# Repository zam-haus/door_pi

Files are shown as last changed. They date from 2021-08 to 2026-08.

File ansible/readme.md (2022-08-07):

# Usage (run as root):
* configure raspi image file (add ssh file in boot partition and add ssh public key to authorized keys file for root and pi user):

		ansible-playbook setup-rpi-image.yml -e file=/home/USER/Downloads/2022-04-04-raspios-bullseye-arm64-lite.img -e key=/home/USER/.ssh/id_rsa.pub -e host=HOSTNAME
Note: /dev/loop0 is used as hard-coded loopback device

* write disk image to sdcard:

		dd if=/home/USER/Downloads/2022-04-04-raspios-bullseye-arm64-lite.img of=/dev/DISK status=progress

* configure read only root

		ansible-playbook setup-rpi-readonly.yml -i HOSTNAME,
Note: the extra comma at the end is not a mistake

* setup client

		ansible-playbook setup-client.yml -i HOSTNAME,

* update client

		ansible-playbook update-client.yml -i HOSTNAME,

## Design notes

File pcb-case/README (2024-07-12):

PI case inspired by https://www.printables.com/de/model/270114-raspberry-pi-4-case

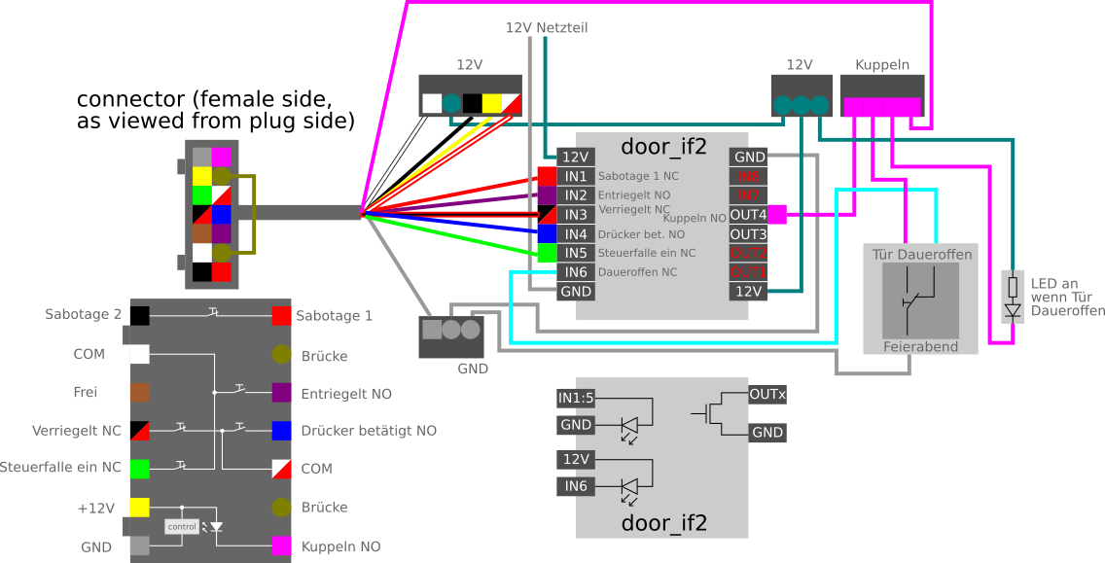
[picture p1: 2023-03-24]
pcb/door_if2/connection-plan-w.switch.png

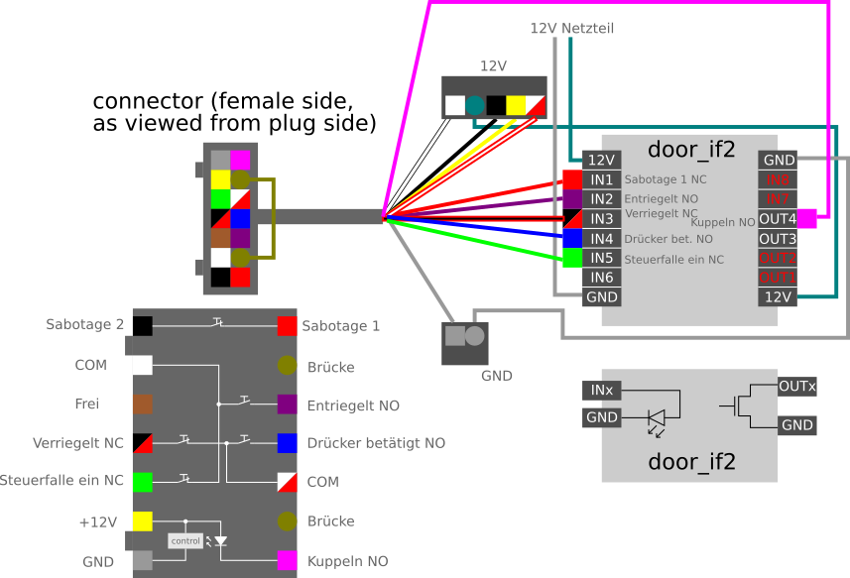
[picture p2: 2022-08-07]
pcb/door_if3_usb/connection-plan.png

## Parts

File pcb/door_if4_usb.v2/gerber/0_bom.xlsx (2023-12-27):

Comment | Designator | Footprint
LY323DC24 | D2,D10,D12,D18,D3,D5,D13,D4,D11 | D_SOD-323
D | D28,D31,D34,D27,D35,D33,D30,D39,D37,D29,D38,D32,D41,D40,D26,D36 | D_SOD-523
SS24B | D24,D7,D22,D9,D16,D25,D8,D23,D17,D14,D15,D6 | D_SMB
10k | R8,R38,R21,R39,R5,R10,R29,R9,R45,R7,R31,R12,R11,R13,R30,R26,R27,R42,R3,R19,R33,R44,R32,R41,R6,R28,R40,R43 | R_0402_1005Metric
2k2 | R60,R54,R17,R55,R20,R49,R66,R52,R64,R56,R47,R18,R16,R46,R57,R63,R68,R15,R50,R48,R14,R62,R65,R58 | R_0402_1005Metric
120 | R22,R4,R2,R24,R36,R34 | R_0402_1005Metric
LTV-247 | U3,U7,U8,U4,U2,U6,U5 | SOP-16_4.4x10.4mm_P1.27mm
IRF7343 | Q4,Q6,Q1,Q5,Q2,Q3 | SO-8_3.9x4.9mm_P1.27mm
100n/50V | C3,C2,C4,C1 | C_0805_2012Metric
LED | D1 | LED_0603_1608Metric
COS2171 | U10,U9 | SOP-8_3.9x4.9mm_P1.27mm
470 | R1 | R_0402_1005Metric

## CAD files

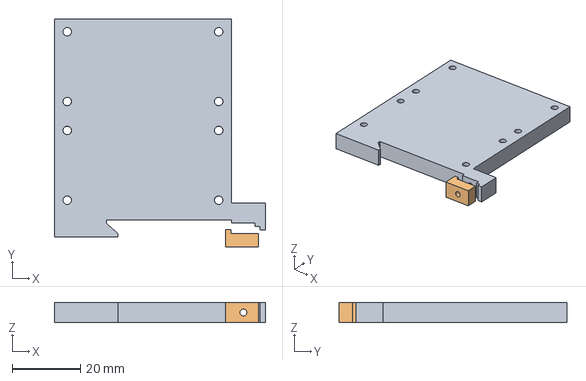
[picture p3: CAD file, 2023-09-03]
extensions/relais/relais_mount.FCStd
62.0 x 67.0 x 6.00 mm
Plate
CounterBlock

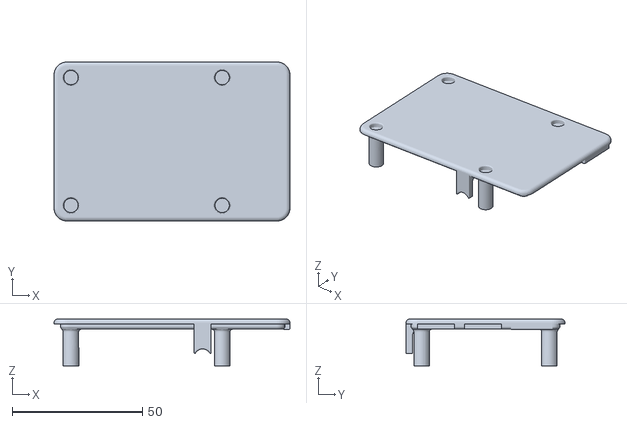
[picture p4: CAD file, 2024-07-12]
pcb-case/General_lit.stl
90.5 x 61.0 x 18.0

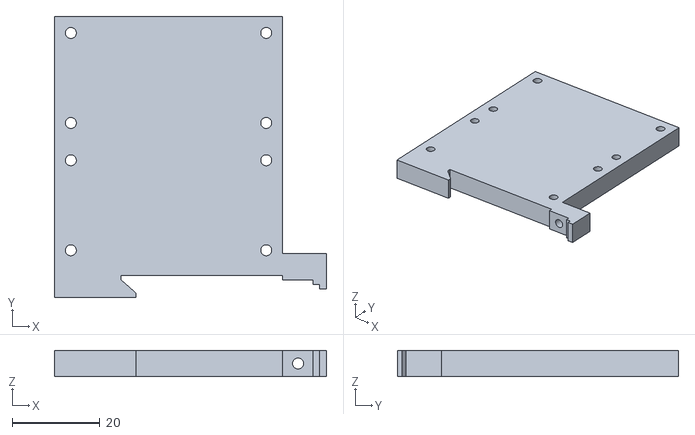
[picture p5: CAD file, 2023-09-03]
extensions/relais/relais_mount-Plate.stl
62.0 x 64.0 x 6.00

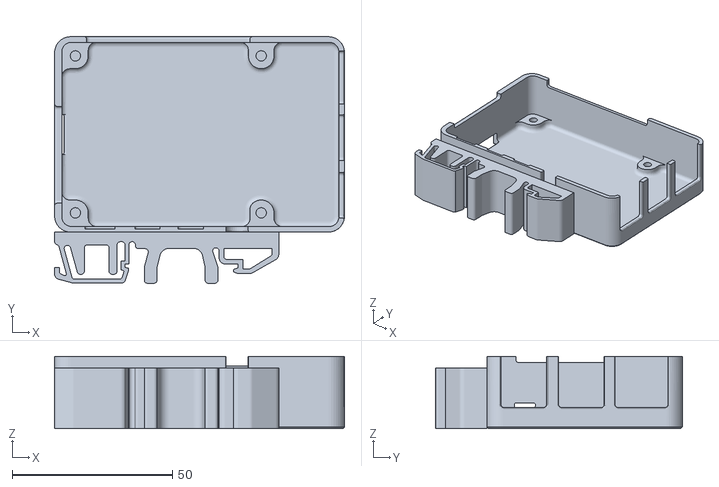
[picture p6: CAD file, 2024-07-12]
pcb-case/Pi4_DIN_case.stl
90.5 x 77.0 x 22.6

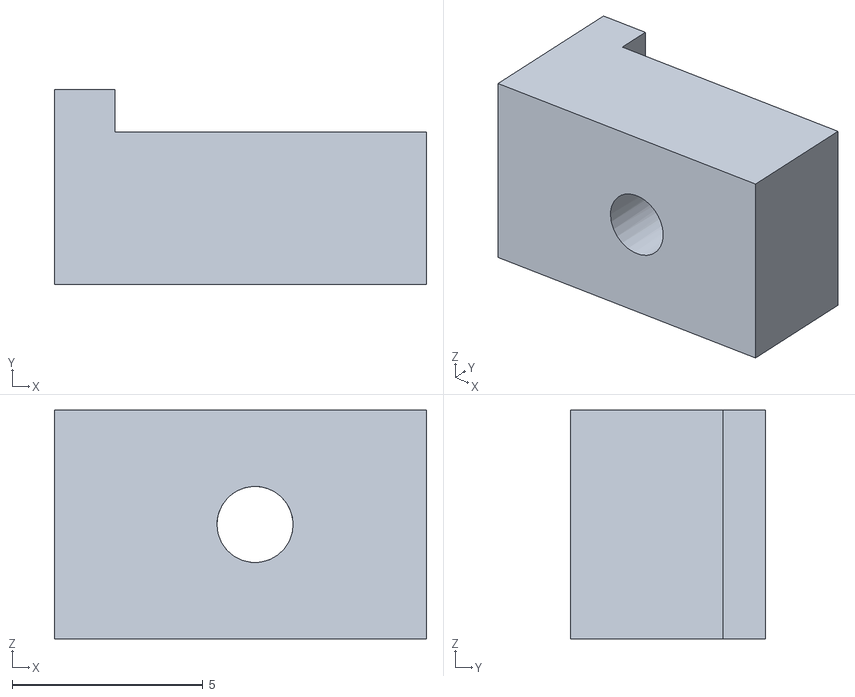
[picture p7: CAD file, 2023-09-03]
extensions/relais/relais_mount-CounterBlock.stl
9.76 x 5.12 x 6.00

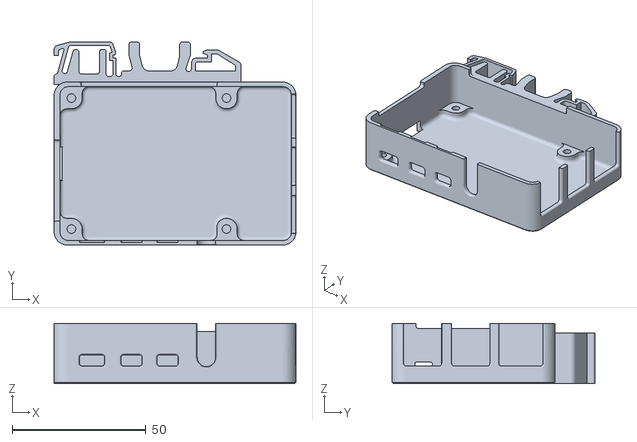
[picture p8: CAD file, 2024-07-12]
pcb-case/Pi4_DIN_case_2.stl
90.5 x 76.0 x 22.6

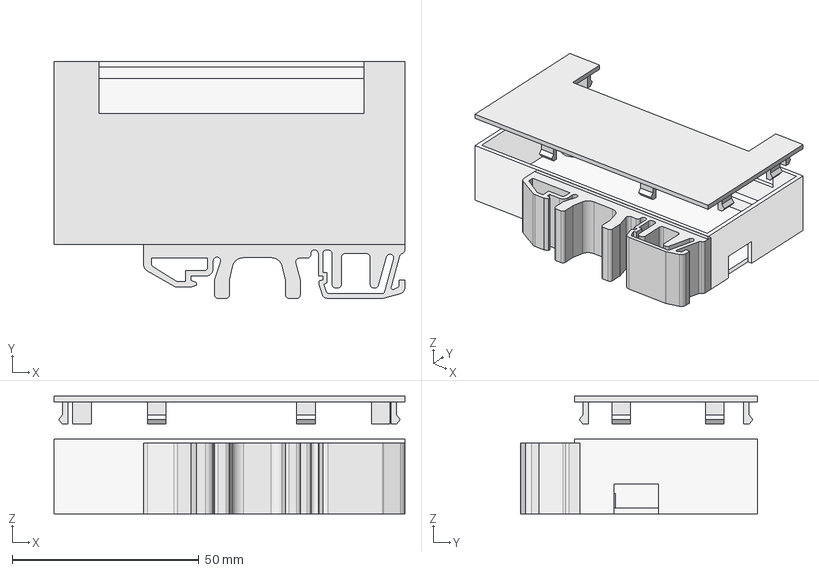
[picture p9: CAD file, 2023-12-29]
pcb-case/if4-usb-case.v2.FCStd
94.0 x 63.5 x 31.5 mm
Body-main
Body-clip
Body-top-complete

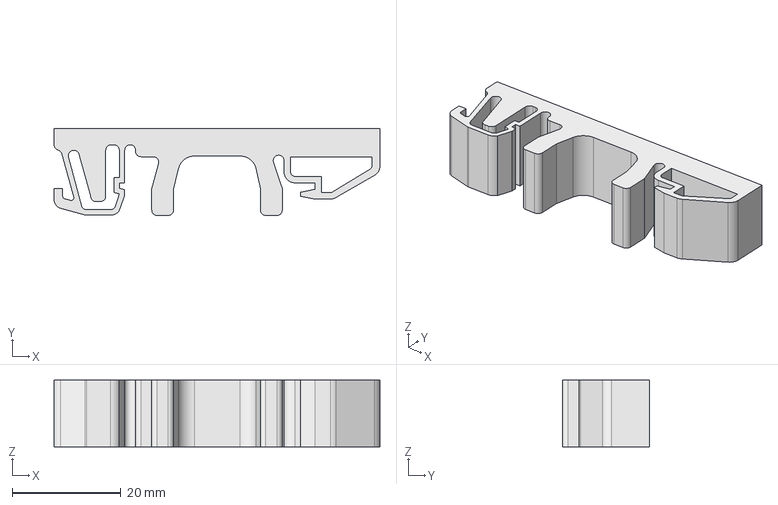
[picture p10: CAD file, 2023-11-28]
pcb-case/DINrail_Clip.fcstd
60.0 x 16.0 x 12.3 mm

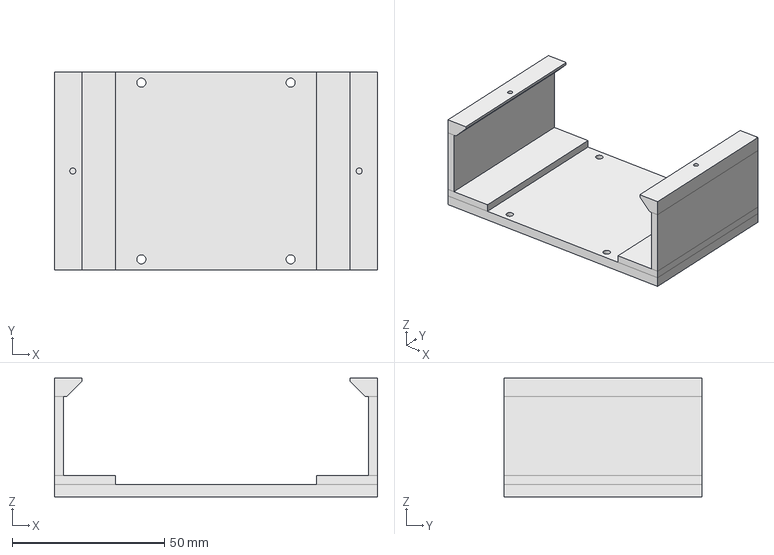
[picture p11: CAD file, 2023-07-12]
pcb-case/raspi-hub-case.FCStd
106.0 x 65.0 x 39.0 mm

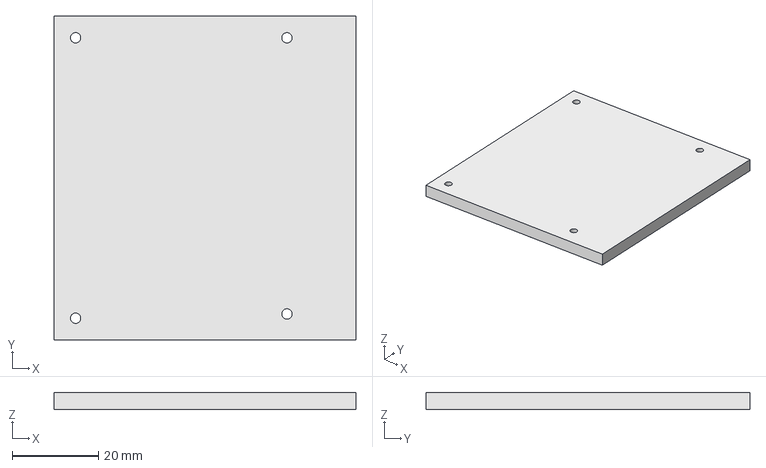
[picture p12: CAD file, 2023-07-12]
pcb-case/if3-usb-case.FCStd
70.0 x 75.0 x 4.00 mm

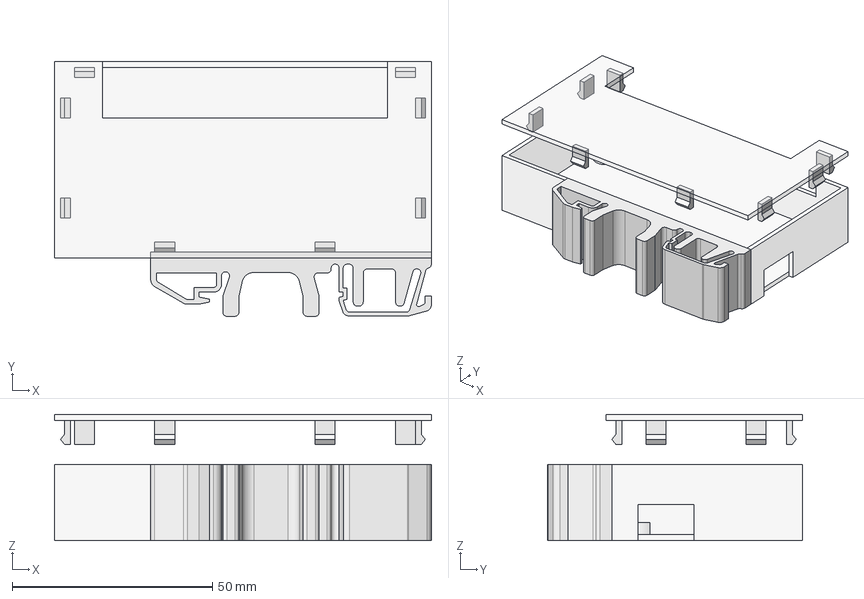
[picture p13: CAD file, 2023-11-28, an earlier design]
pcb-case/if4-usb-case.FCStd
94.0 x 63.5 x 31.5 mm
Body-main
Body-clip
Body-top
Body-top-clip
Body-top-clip-2
Body-top-clip-3
Body-top-clip-4
Body-top-clip-5
Body-top-clip-6
Body-top-clip-7
Body-top-clip-8

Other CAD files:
pcb-case/DINrail_Clip.stl
pcb-case/if4-usb-case.v2.stl

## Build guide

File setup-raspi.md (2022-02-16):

# Raspi Setup

## Hardware

* Raspberry PI 4B (2 GB)
* PoE+ Hat for RasPi 4 Model B (25 W)
* door_if Hat

## Raspi Configuration

### PoE Fan Control

*/boot/config.txt (section [all]):*

	dtparam=poe_fan_temp0=60000
	dtparam=poe_fan_temp1=65000
	dtparam=poe_fan_temp2=70000
	dtparam=poe_fan_temp3=75000

### Disable WLAN and Bluetooth

*/boot/config.txt (general section):*
	dtoverlay=disable-wifi
	dtoverlay=disable-bt

### Read-Only Filesystem

*according to* [c't 26/2021](https://www.heise.de/select/ct/2021/16/2112313321295857638) 

* install network-manager:

		apt-get install network-manager
		systemctl enable --now NetworkManager
		cd /etc
		ln -sf ../run/NetworkManager/resolv.conf
		
* configure kernel boot in /boot/cmdline.txt
    * ... root=... **ro** rootfstype=ext4 ...
* configure filesystems in /etc/fstab
    * ... /boot vfat ro,defaults ...
    * ... / ext4 ro,defaults,noatime ...
* add tmpfs in /etc/fstab:

		tmpfs           /var/lib/systemd   tmpfs     mode=0755               0 0
		tmpfs           /var/lib/private   tmpfs     mode=0700               0 0
		tmpfs           /var/log           tmpfs     nodev,nosuid            0 0
		tmpfs           /var/tmp           tmpfs     nodev,nosuid            0 0
		tmpfs           /var/cache         tmpfs     nodev,nosuid            0 0
		tmpfs           /tmp               tmpfs     nodev,nosuid,mode=1777  0 0

* disable swap

		systemctl disable dphys-swapfile

* shell highlighting /root/.bashrc

		export LS_OPTIONS='--color=auto'
		eval "`dircolors`"
		alias ls='ls $LS_OPTIONS'
		alias ll='ls $LS_OPTIONS -la'
		alias l='ls $LS_OPTIONS'
		set_bash_prompt() {
			fs_mode=$(mount | sed -n -e "s/^\/dev\/.* on \/ .*(\(r[w|o]\).*/\1/p")
			PS1='\[\033[01;31m\]\u@\h${fs_mode:+($fs_mode)}\[\033[00m\]:\[\033[01;34m\]\w\[\033[00m\]\$ '
		}
		alias ro='sudo mount -o remount,ro / ; sudo mount -o remount,ro /boot'
		alias rw='sudo mount -o remount,rw / ; sudo mount -o remount,rw /boot'
		PROMPT_COMMAND=set_bash_prompt

* shell highlighting /home/pi/.bashrc

		export LS_OPTIONS='--color=auto'
		eval "`dircolors`"
		alias ls='ls $LS_OPTIONS'
		alias ll='ls $LS_OPTIONS -la'
		alias l='ls $LS_OPTIONS'
		set_bash_prompt() {
			fs_mode=$(mount | sed -n -e "s/^\/dev\/.* on \/ .*(\(r[w|o]\).*/\1/p")
			PS1='\[\033[01;32m\]\u@\h${fs_mode:+($fs_mode)}\[\033[00m\]:\[\033[01;34m\]\w\[\033[00m\]\$ '
		}
		alias ro='sudo mount -o remount,ro / ; sudo mount -o remount,ro /boot'
		alias rw='sudo mount -o remount,rw / ; sudo mount -o remount,rw /boot'
		PROMPT_COMMAND=set_bash_prompt

### Setup Door Manager on Raspi

* install python3-pip and pipenv

		sudo apt install python3-pip
		sudo pip3 install pipenv

* copy door_manager dir to /home/pi

* copy door_manager/config.json.example to door_manager/config.json

* adjust config.json settings according to your setup

* setup pipenv

		cd /home/pi/door_manager
		pipenv install --site-packages

* setup systemd service

		sudo cp /home/pi/door_manager/door-manager.service /etc/systemd/system/
		sudo systemctl daemon-reload
		sudo systemctl enable door-manager
		sudo systemctl start door-manager

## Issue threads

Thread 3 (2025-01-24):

Nach einem Netzwerkausfall gehts nicht mehr (dauerhaft)

cod3monk, 2025-01-24:
Wir hatten heute einen Stromausfall beim Netzwerkzeugs im Haupthaus, der Doorpi im Seminarraum selbst war davon nicht betroffen. Danach ging der Hintereingang nicht mehr per Sesam und kam auch nicht automatisch wieder hoch als Netzwerk wieder funktioniert hatte. Ein powercycle vom doorpi hat geholfen.

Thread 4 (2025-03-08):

Reset des USB Devices wird nicht erkannt

chca42, 2025-03-08:
Der door_manager bleibt hängen, wenn das USB-Device resettet, weil er weder den Reset erkennt noch abstürzt.

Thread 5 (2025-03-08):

Konfiguration verteilt auf USB-HAL und doorpi

TheJonny, 2025-03-08:
Die der picopi in der USB-HAL-Platine hat eine seperate Konfigurationsdatei, wo logisch H/L auf Elektrisch H/L/Z zugeordnet wird. Hier wäre es schön, wenn das nur in der  config.json in door_pi konfiguriert würde, damit sich alle USB-HAL-Platinen gleich immer verhalten.

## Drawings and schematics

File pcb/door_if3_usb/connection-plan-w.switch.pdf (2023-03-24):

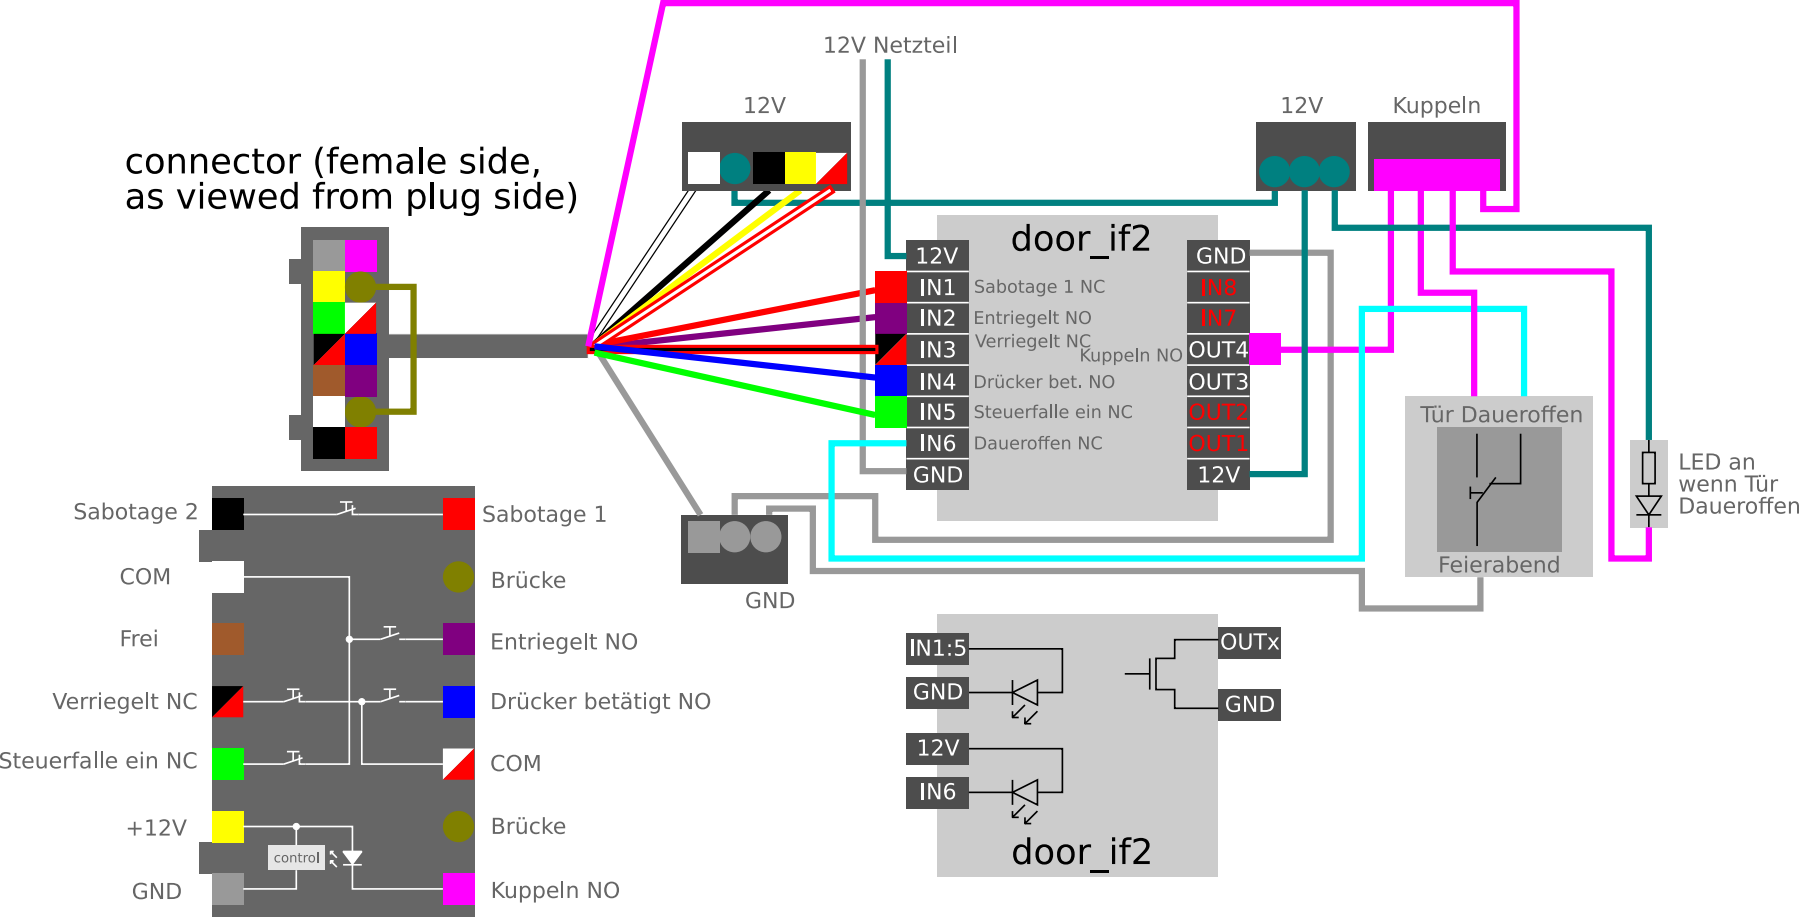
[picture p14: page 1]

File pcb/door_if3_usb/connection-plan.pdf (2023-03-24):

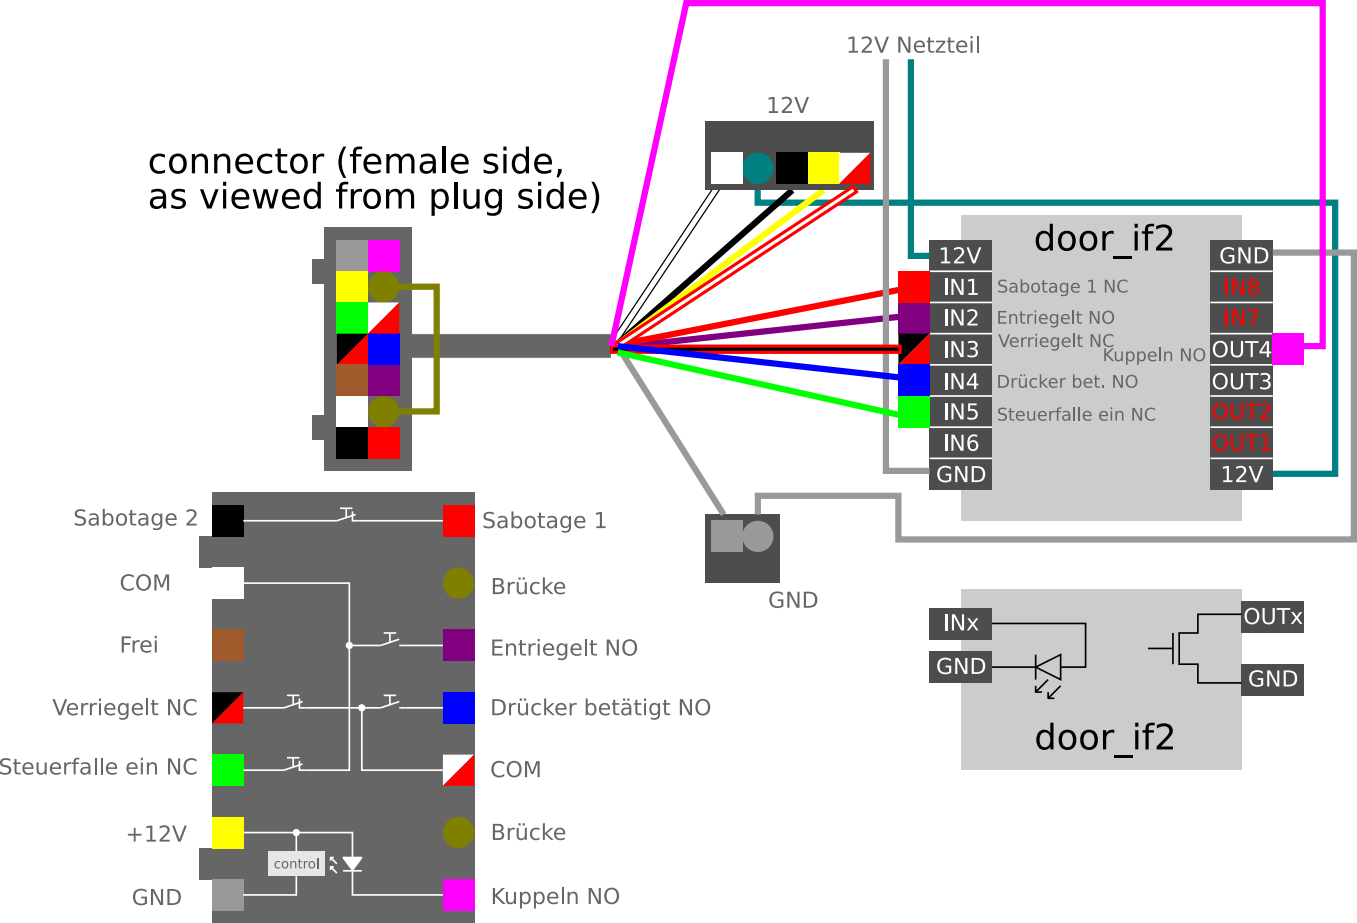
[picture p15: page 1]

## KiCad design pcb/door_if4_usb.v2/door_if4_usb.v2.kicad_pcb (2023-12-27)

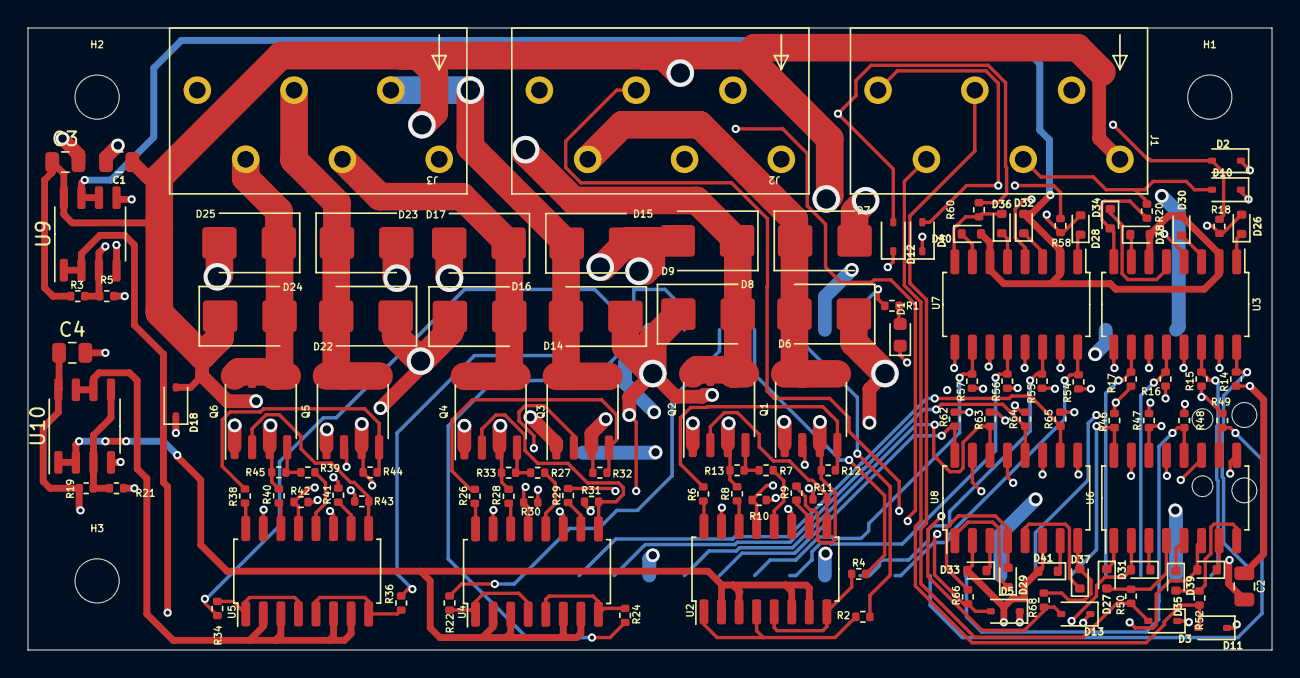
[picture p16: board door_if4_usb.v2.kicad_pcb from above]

Board: 4 copper layers, 90.0 x 45.0 mm, 123 parts (1 on the bottom side), 102 nets.

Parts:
C1, C2, C3, C4: 100n/50V; C_0805_2012Metric
D1: LED; LED_0603_1608Metric
D2, D3, D4, D5, D10, D11, D12, D13, D18: LY323DC24; D_SOD-323
D6, D7, D8, D9, D14, D15, D16, D17, D22, D23, D24, D25: SS24B; D_SMB
D26, D27, D28, D29, D30, D31, D32, D33, D34, D35, D36, D37, D38, D39, D40, D41: D; D_SOD-523
H1, H2, H3: MountingHole; MountingHole_3.2mm_M3_DIN965
J1, J2, J3: WAGO 250-206; WAGO-250-206
Q1, Q2, Q3, Q4, Q5, Q6: IRF7343; SO-8_3.9x4.9mm_P1.27mm
R1: 470; R_0402_1005Metric
R2, R4, R22, R24, R34, R36: 120; R_0402_1005Metric
R3, R5, R6, R7, R8, R9, R10, R11, R12, R13, R19, R21, R26, R27, R28, R29, R30, R31, R32, R33, R38, R39, R40, R41, R42, R43, R44, R45: 10k; R_0402_1005Metric
R14, R15, R16, R17, R18, R20, R46, R47, R48, R49, R50, R52, R54, R55, R56, R57, R58, R60, R62, R63, R64, R65, R66, R68: 2k2; R_0402_1005Metric
U1: Pico; RPi_Pico_SMDonly
U2, U3, U4, U5, U6, U7, U8: LTV-247; SOP-16_4.4x10.4mm_P1.27mm
U9, U10: COS2171; SOP-8_3.9x4.9mm_P1.27mm

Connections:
+3V3: C2.1, C4.1, R14.1, R15.1, R16.1, R17.1, R19.1, R46.1, R47.1, R48.1, R49.1, R54.1, R55.1, R56.1, R57.1, R62.1, R63.1, R64.1, R65.1, U1.36 (3V3), U10.8 (V+)
+24V: C1.1, C3.1, D6.1 (K), D8.1 (K), D14.1 (K), D16.1 (K), D18.2 (A2), D22.1 (K), D24.1 (K), J1.1, J2.1, Q1.3 (S2), Q2.3 (S2), Q3.3 (S2), Q4.3 (S2), Q5.3 (S2), Q6.3 (S2), R3.1, R8.2, R9.2, R12.2, R13.2, R28.2, R29.2, R32.2, R33.2, R40.2, R41.2, R44.2, R45.2, U9.8 (V+)
GND: C2.2, C4.2, D1.1 (K), R21.2, U1.3 (GND), U1.8 (GND), U1.13 (GND), U1.18 (GND), U1.23 (GND), U1.28 (GND), U1.38 (GND), U1.42 (GND), U3.9, U3.11, U3.13, U3.15, U6.9, U6.11, U6.13, U6.15, U7.9, U7.11, U7.13, U7.15, U8.9, U8.11, U8.13, U8.15, U10.4 (V-)
GNDA: C1.2, C3.2, D2.1 (A1), D3.1 (A1), D4.1 (A1), D5.1 (A1), D7.2 (A), D9.2 (A), D10.1 (A1), D11.1 (A1), D12.1 (A1), D13.1 (A1), D15.2 (A), D17.2 (A), D18.1 (A1), D23.2 (A), D25.2 (A), J2.6, J3.6, Q1.1 (S1), Q2.1 (S1), Q3.1 (S1), Q4.1 (S1), Q5.1 (S1), Q6.1 (S1), R5.2, R10.1, R11.1, R30.1, R31.1, R42.1, R43.1, U2.11, U2.15, U4.11, U4.15, U5.11, U5.15, U9.4 (V-)
IN1: D2.2 (A2), J1.2, R18.2
IN2: D10.2 (A2), J1.3, R20.2
IN3: D3.2 (A2), J1.4, R50.2
IN4: D11.2 (A2), J1.5, R52.2
IN5: D4.2 (A2), J1.6, R58.2
IN6: D12.2 (A2), J2.2, R60.2
IN7: D5.2 (A2), J2.3, R66.2
IN8: D13.2 (A2), J2.4, R68.2
unnamed: D1.2 (A), R1.1
unnamed: D26.2 (A), R18.1, U3.4
unnamed: D26.1 (K), U3.1
unnamed: D27.2 (A), R50.1, U6.4
unnamed: D27.1 (K), U6.1
unnamed: D28.2 (A), R58.1, U7.4
unnamed: D28.1 (K), U7.1
unnamed: D29.2 (A), R66.1, U8.4
unnamed: D29.1 (K), U8.1
unnamed: D30.1 (K), U3.3
unnamed: D31.1 (K), U6.3
unnamed: D32.1 (K), U7.3
unnamed: D33.1 (K), U8.3
unnamed: D34.2 (A), R20.1, U3.8
unnamed: D34.1 (K), U3.5
unnamed: D35.2 (A), R52.1, U6.8
unnamed: D35.1 (K), U6.5
unnamed: D36.2 (A), R60.1, U7.8
unnamed: D36.1 (K), U7.5
unnamed: D37.2 (A), R68.1, U8.8
unnamed: D37.1 (K), U8.5
unnamed: D38.1 (K), U3.7
unnamed: D39.1 (K), U6.7
unnamed: D40.1 (K), U7.7
unnamed: D41.1 (K), U8.7
unnamed: Q1.2 (G1), R10.2, U2.13
unnamed: Q1.4 (G2), R6.2, R12.1
unnamed: Q2.2 (G1), R11.2, U2.9
unnamed: Q2.4 (G2), R7.2, R13.1
unnamed: Q3.2 (G1), R30.2, U4.13
unnamed: Q3.4 (G2), R26.2, R32.1
unnamed: Q4.2 (G1), R31.2, U4.9
unnamed: Q4.4 (G2), R27.2, R33.1
unnamed: Q5.2 (G1), R42.2, U5.13
unnamed: Q5.4 (G2), R38.2, R44.1
unnamed: Q6.2 (G1), R43.2, U5.9
unnamed: Q6.4 (G2), R39.2, R45.1
unnamed: R2.2, U2.1, U2.4
unnamed: R4.2, U2.5, U2.8
unnamed: R6.1, U2.16
unnamed: R7.1, U2.12
unnamed: R8.1, U2.14
unnamed: R9.1, U2.10
unnamed: R22.2, U4.1, U4.4
unnamed: R24.2, U4.5, U4.8
unnamed: R26.1, U4.16
unnamed: R27.1, U4.12
unnamed: R28.1, U4.14
unnamed: R29.1, U4.10
unnamed: R34.2, U5.1, U5.4
unnamed: R36.2, U5.5, U5.8
unnamed: R38.1, U5.16
unnamed: R39.1, U5.12
unnamed: R40.1, U5.14
unnamed: R41.1, U5.10
unnamed: R3.2, R5.1, U9.3 (+), U9.5 (+)
unnamed: R19.2, R21.1, U10.3 (+), U10.5 (+)
OUT1: D6.2 (A), D7.1 (K), J2.5, Q1.5 (D), Q1.6 (D), Q1.7 (D), Q1.8 (D)
OUT2: D8.2 (A), D9.1 (K), J3.1, Q2.5 (D), Q2.6 (D), Q2.7 (D), Q2.8 (D)
OUT3: D14.2 (A), D15.1 (K), J3.2, Q3.5 (D), Q3.6 (D), Q3.7 (D), Q3.8 (D)
OUT4: D16.2 (A), D17.1 (K), J3.3, Q4.5 (D), Q4.6 (D), Q4.7 (D), Q4.8 (D)
OUT5: D22.2 (A), D23.1 (K), J3.4, Q5.5 (D), Q5.6 (D), Q5.7 (D), Q5.8 (D)
OUT6: D24.2 (A), D25.1 (K), J3.5, Q6.5 (D), Q6.6 (D), Q6.7 (D), Q6.8 (D)
O_LED: R1.2, U1.29 (GPIO22)
S_IN1A: R14.2, U1.1 (GPIO0), U3.16
S_IN1B: R15.2, U1.2 (GPIO1), U3.14
S_IN2A: R16.2, U1.4 (GPIO2), U3.12
S_IN2B: R17.2, U1.5 (GPIO3), U3.10
S_IN3A: R46.2, U1.6 (GPIO4), U6.16
S_IN3B: R47.2, U1.7 (GPIO5), U6.14
S_IN4A: R48.2, U1.9 (GPIO6), U6.12
S_IN4B: R49.2, U1.10 (GPIO7), U6.10
S_IN5A: R54.2, U1.11 (GPIO8), U7.16
S_IN5B: R55.2, U1.12 (GPIO9), U7.14
S_IN6A: R56.2, U1.14 (GPIO10), U7.12
S_IN6B: R57.2, U1.15 (GPIO11), U7.10
S_IN7A: R62.2, U1.16 (GPIO12), U8.16
S_IN7B: R63.2, U1.17 (GPIO13), U8.14
S_IN8A: R64.2, U1.19 (GPIO14), U8.12
S_IN8B: R65.2, U1.20 (GPIO15), U8.10
S_OUT1: R2.1, U1.27 (GPIO21)
S_OUT2: R4.1, U1.26 (GPIO20)
S_OUT3: R22.1, U1.25 (GPIO19)
S_OUT4: R24.1, U1.24 (GPIO18)
S_OUT5: R34.1, U1.22 (GPIO17)
S_OUT6: R36.1, U1.21 (GPIO16)
VmidA: D31.2 (A), D33.2 (A), D39.2 (A), D41.2 (A), U6.2, U6.6, U8.2, U8.6, U9.1, U9.2 (-)
VmidB: D30.2 (A), D32.2 (A), D38.2 (A), D40.2 (A), U3.2, U3.6, U7.2, U7.6, U9.6 (-), U9.7
Vmid_3v3_A: U2.2, U2.3, U2.6, U2.7, U4.2, U4.3, U4.6, U4.7, U10.1, U10.2 (-)
Vmid_3v3_B: U5.2, U5.3, U5.6, U5.7, U10.6 (-), U10.7

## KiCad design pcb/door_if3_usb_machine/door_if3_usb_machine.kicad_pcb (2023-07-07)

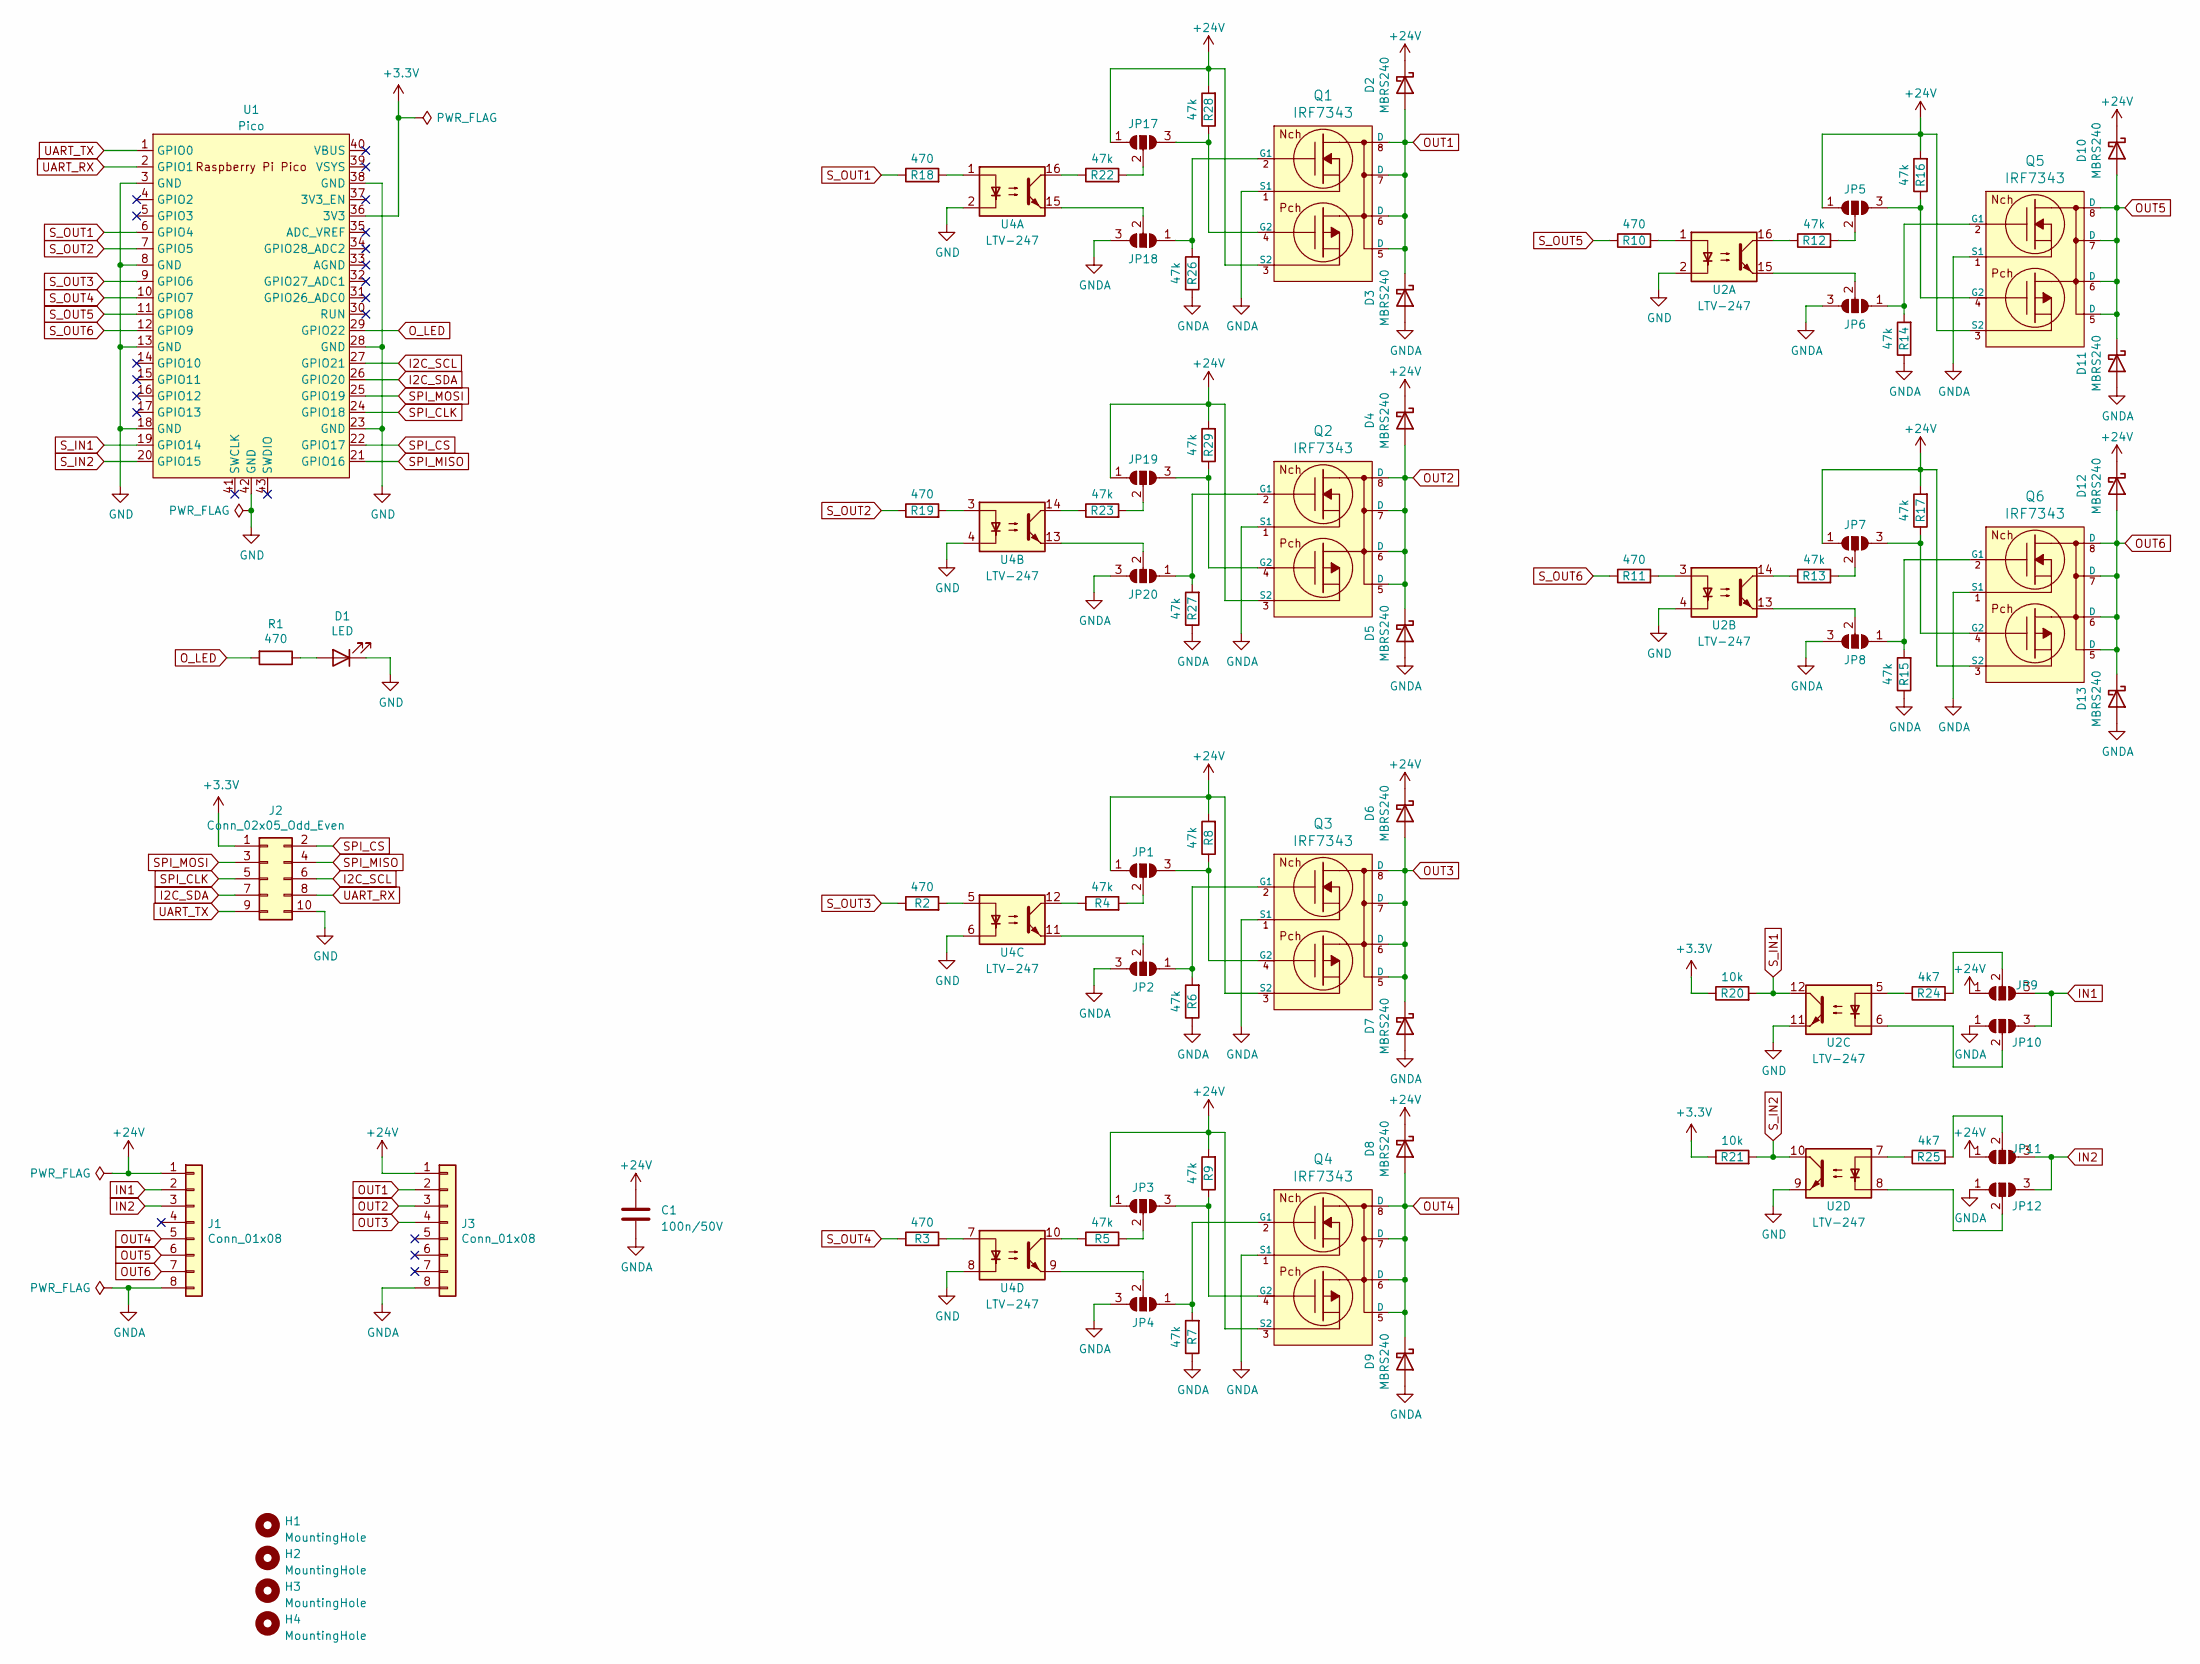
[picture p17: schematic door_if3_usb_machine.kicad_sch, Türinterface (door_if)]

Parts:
C1: 100n/50V; C_0603_1608Metric_Pad1.08x0.95mm_HandSolder
D1: LED; LED_0603_1608Metric_Pad1.05x0.95mm_HandSolder
D2, D3, D4, D5, D6, D7, D8, D9, D10, D11, D12, D13: MBRS240; D_SMB_Handsoldering
H1, H2, H3, H4: MountingHole; MountingHole_3.2mm_M3_DIN965
J1, J3: Conn_01x08; LSA-IDC381-8
J2: Conn_02x05_Odd_Even; con-harting-ml-ML10
JP1, JP2, JP3, JP4, JP5, JP6, JP7, JP8, JP9, JP10, JP11, JP12, JP17, JP18, JP19, JP20: SolderJumper_3_Open; SolderJumper-3_P1.3mm_Open_Pad1.0x1.5mm
Q1, Q2, Q3, Q4, Q5, Q6: IRF7343; SO-8_3.9x4.9mm_P1.27mm
R1, R2, R3, R10, R11, R18, R19: 470; R_0603_1608Metric_Pad0.98x0.95mm_HandSolder
R4, R5, R6, R7, R8, R9, R12, R13, R14, R15, R16, R17, R22, R23, R26, R27, R28, R29: 47k; R_0603_1608Metric_Pad0.98x0.95mm_HandSolder
R20, R21: 10k; R_0603_1608Metric_Pad0.98x0.95mm_HandSolder
R24, R25: 4k7; R_0603_1608Metric_Pad0.98x0.95mm_HandSolder
U1: Pico; RPi_Pico_SMDonly
U2, U4: LTV-247; SOP-16_4.4x10.4mm_P1.27mm

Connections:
+3V3: J2.1, R20.1, R21.1, U1.36 (3V3)
+24V: C1.1, D2.1 (K), D4.1 (K), D6.1 (K), D8.1 (K), D10.1 (K), D12.1 (K), J1.1, J3.1, JP1.1 (A), JP3.1 (A), JP5.1 (A), JP7.1 (A), JP9.1 (A), JP11.1 (A), JP17.1 (A), JP19.1 (A), Q1.3 (S2), Q2.3 (S2), Q3.3 (S2), Q4.3 (S2), Q5.3 (S2), Q6.3 (S2), R8.2, R9.2, R16.2, R17.2, R28.2, R29.2
GND: D1.1 (K), J2.10, U1.3 (GND), U1.8 (GND), U1.13 (GND), U1.18 (GND), U1.23 (GND), U1.28 (GND), U1.38 (GND), U1.42 (GND), U2.2, U2.4, U2.9, U2.11, U4.2, U4.4, U4.6, U4.8
GNDA: C1.2, D3.2 (A), D5.2 (A), D7.2 (A), D9.2 (A), D11.2 (A), D13.2 (A), J1.8, J3.8, JP2.3 (B), JP4.3 (B), JP6.3 (B), JP8.3 (B), JP10.1 (A), JP12.1 (A), JP18.3 (B), JP20.3 (B), Q1.1 (S1), Q2.1 (S1), Q3.1 (S1), Q4.1 (S1), Q5.1 (S1), Q6.1 (S1), R6.1, R7.1, R14.1, R15.1, R26.1, R27.1
I2C_SCL: J2.6, U1.27 (GPIO21)
I2C_SDA: J2.7, U1.26 (GPIO20)
IN1: J1.2, JP9.3 (B), JP10.3 (B)
IN2: J1.3, JP11.3 (B), JP12.3 (B)
unnamed: D1.2 (A), R1.1
unnamed: JP1.3 (B), Q3.4 (G2), R8.1
unnamed: JP1.2 (C), R4.2
unnamed: JP2.1 (A), Q3.2 (G1), R6.2
unnamed: JP2.2 (C), U4.11
unnamed: JP3.3 (B), Q4.4 (G2), R9.1
unnamed: JP3.2 (C), R5.2
unnamed: JP4.1 (A), Q4.2 (G1), R7.2
unnamed: JP4.2 (C), U4.9
unnamed: JP5.3 (B), Q5.4 (G2), R16.1
unnamed: JP5.2 (C), R12.2
unnamed: JP6.1 (A), Q5.2 (G1), R14.2
unnamed: JP6.2 (C), U2.15
unnamed: JP7.3 (B), Q6.4 (G2), R17.1
unnamed: JP7.2 (C), R13.2
unnamed: JP8.1 (A), Q6.2 (G1), R15.2
unnamed: JP8.2 (C), U2.13
unnamed: JP9.2 (C), R24.2
unnamed: JP10.2 (C), U2.6
unnamed: JP11.2 (C), R25.2
unnamed: JP12.2 (C), U2.8
unnamed: JP17.3 (B), Q1.4 (G2), R28.1
unnamed: JP17.2 (C), R22.2
unnamed: JP18.1 (A), Q1.2 (G1), R26.2
unnamed: JP18.2 (C), U4.15
unnamed: JP19.3 (B), Q2.4 (G2), R29.1
unnamed: JP19.2 (C), R23.2
unnamed: JP20.1 (A), Q2.2 (G1), R27.2
unnamed: JP20.2 (C), U4.13
unnamed: R2.2, U4.5
unnamed: R3.2, U4.7
unnamed: R4.1, U4.12
unnamed: R5.1, U4.10
unnamed: R10.2, U2.1
unnamed: R11.2, U2.3
unnamed: R12.1, U2.16
unnamed: R13.1, U2.14
unnamed: R18.2, U4.1
unnamed: R19.2, U4.3
unnamed: R22.1, U4.16
unnamed: R23.1, U4.14
unnamed: R24.1, U2.5
unnamed: R25.1, U2.7
OUT1: D2.2 (A), D3.1 (K), J3.2, Q1.5 (D), Q1.6 (D), Q1.7 (D), Q1.8 (D)
OUT2: D4.2 (A), D5.1 (K), J3.3, Q2.5 (D), Q2.6 (D), Q2.7 (D), Q2.8 (D)
OUT3: D6.2 (A), D7.1 (K), J3.4, Q3.5 (D), Q3.6 (D), Q3.7 (D), Q3.8 (D)
OUT4: D8.2 (A), D9.1 (K), J1.5, Q4.5 (D), Q4.6 (D), Q4.7 (D), Q4.8 (D)
OUT5: D10.2 (A), D11.1 (K), J1.6, Q5.5 (D), Q5.6 (D), Q5.7 (D), Q5.8 (D)
OUT6: D12.2 (A), D13.1 (K), J1.7, Q6.5 (D), Q6.6 (D), Q6.7 (D), Q6.8 (D)
O_LED: R1.2, U1.29 (GPIO22)
SPI_CLK: J2.5, U1.24 (GPIO18)
SPI_CS: J2.2, U1.22 (GPIO17)
SPI_MISO: J2.4, U1.21 (GPIO16)
SPI_MOSI: J2.3, U1.25 (GPIO19)
S_IN1: R20.2, U1.19 (GPIO14), U2.12
S_IN2: R21.2, U1.20 (GPIO15), U2.10
S_OUT1: R18.1, U1.6 (GPIO4)
S_OUT2: R19.1, U1.7 (GPIO5)
S_OUT3: R2.1, U1.9 (GPIO6)
S_OUT4: R3.1, U1.10 (GPIO7)
S_OUT5: R10.1, U1.11 (GPIO8)
S_OUT6: R11.1, U1.12 (GPIO9)
UART_RX: J2.8, U1.2 (GPIO1)
UART_TX: J2.9, U1.1 (GPIO0)

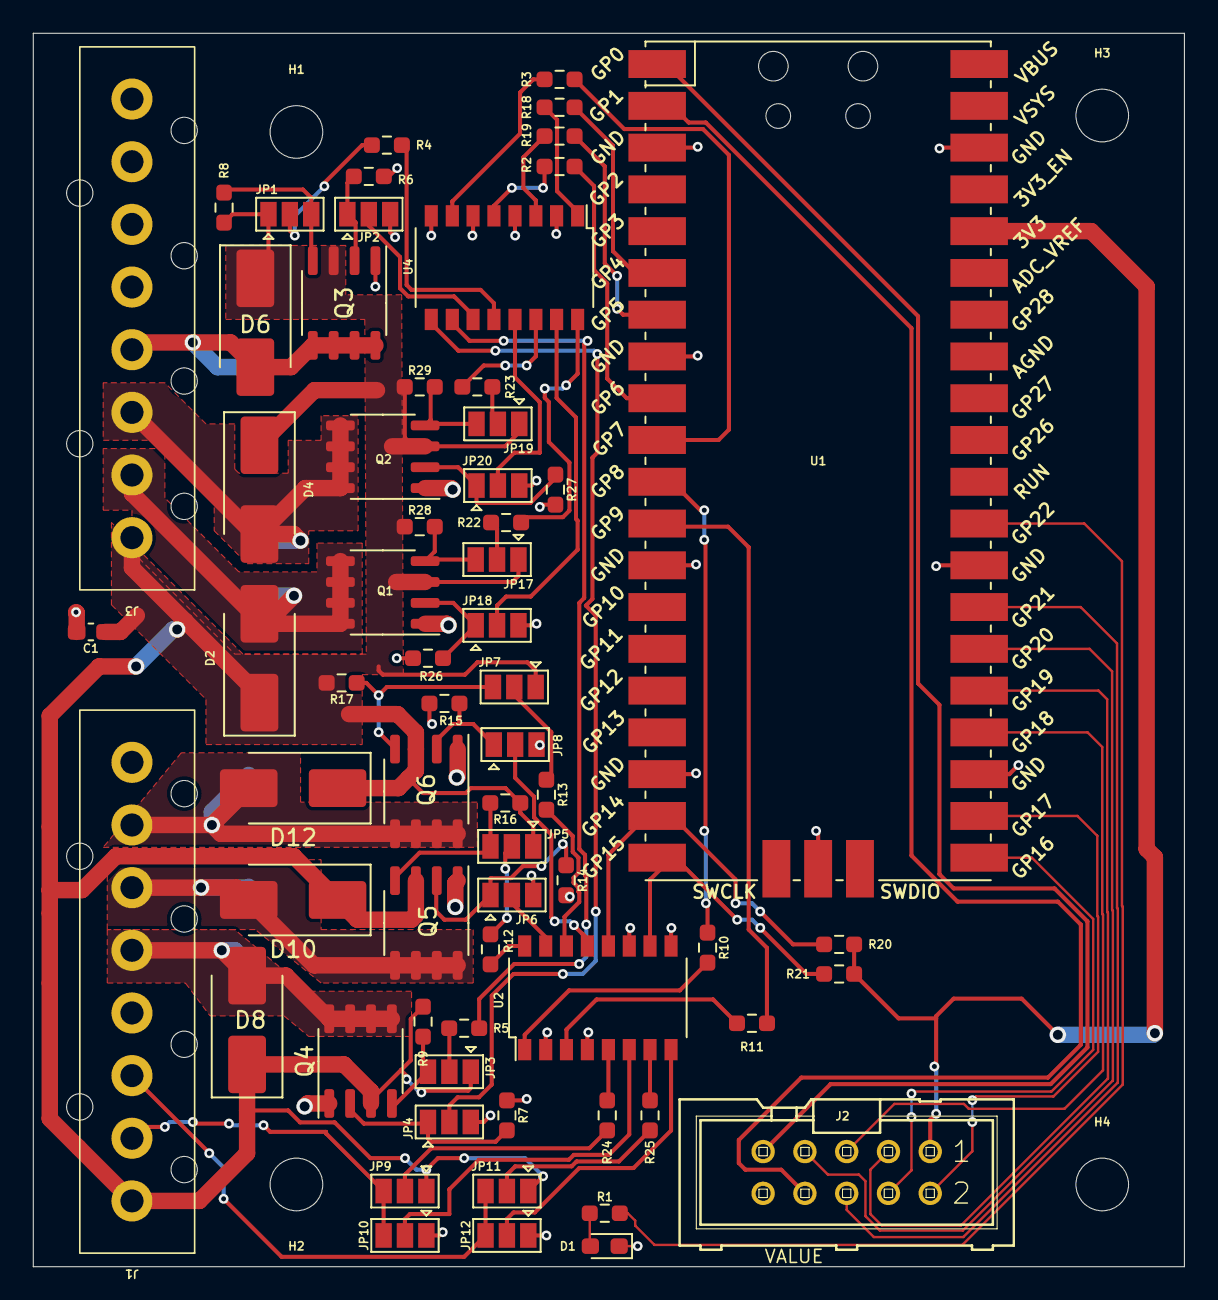
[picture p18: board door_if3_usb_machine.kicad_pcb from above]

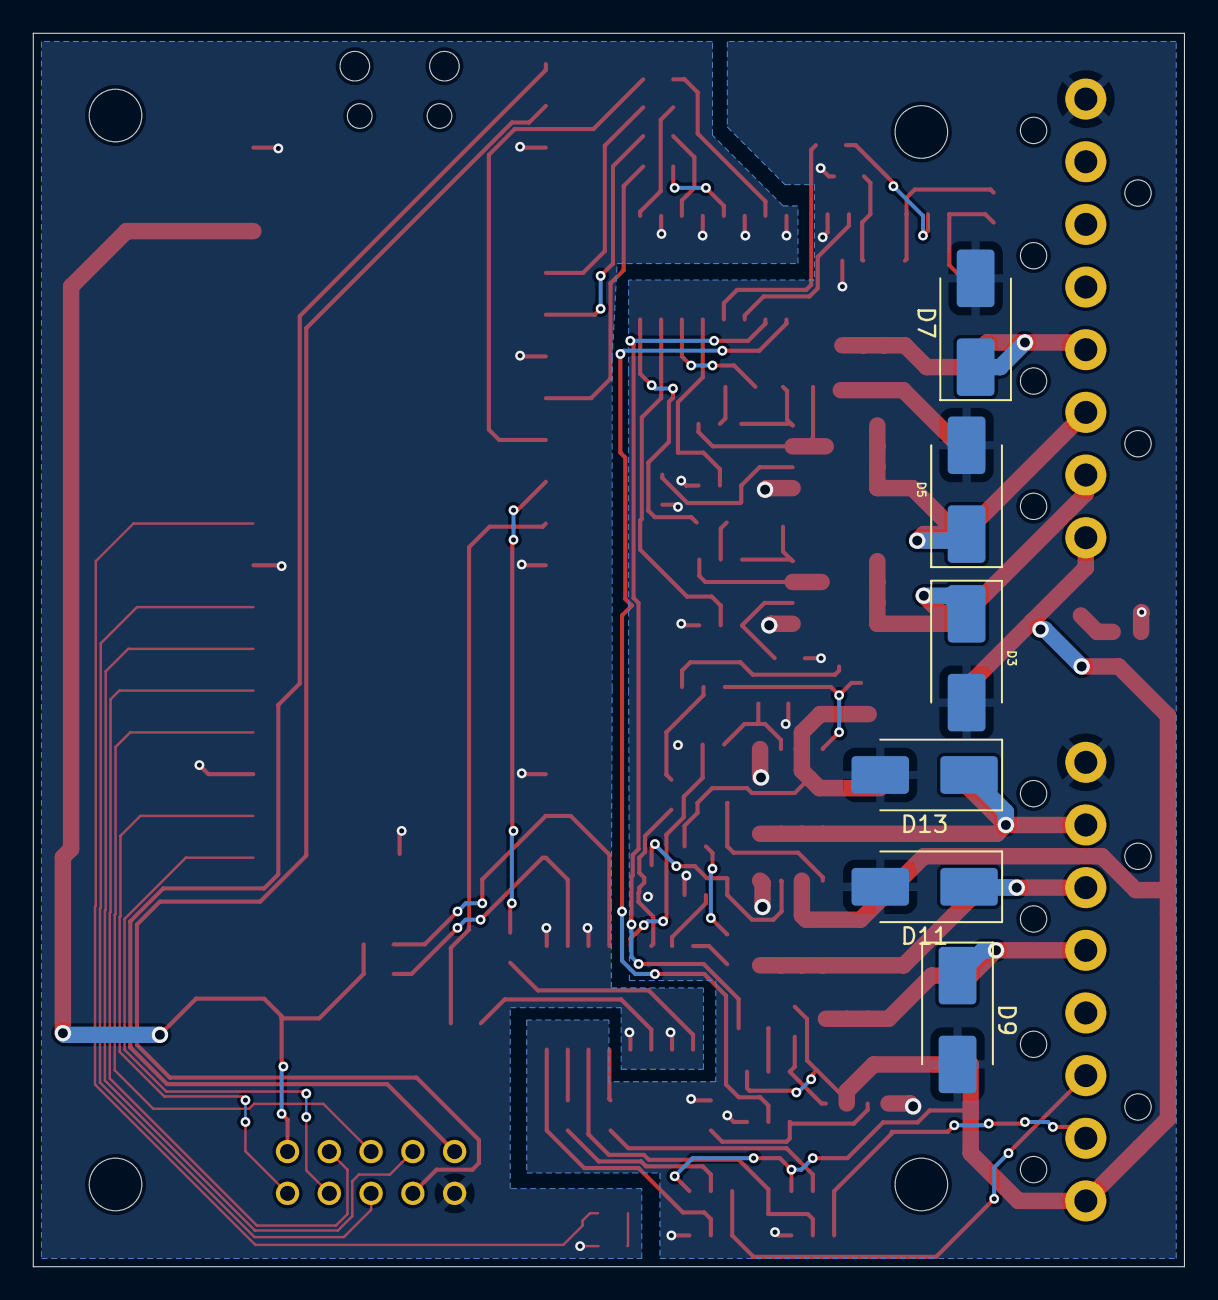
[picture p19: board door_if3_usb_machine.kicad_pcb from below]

Board: 2 copper layers, 70.0 x 75.0 mm, 75 parts (6 on the bottom side), 72 nets.

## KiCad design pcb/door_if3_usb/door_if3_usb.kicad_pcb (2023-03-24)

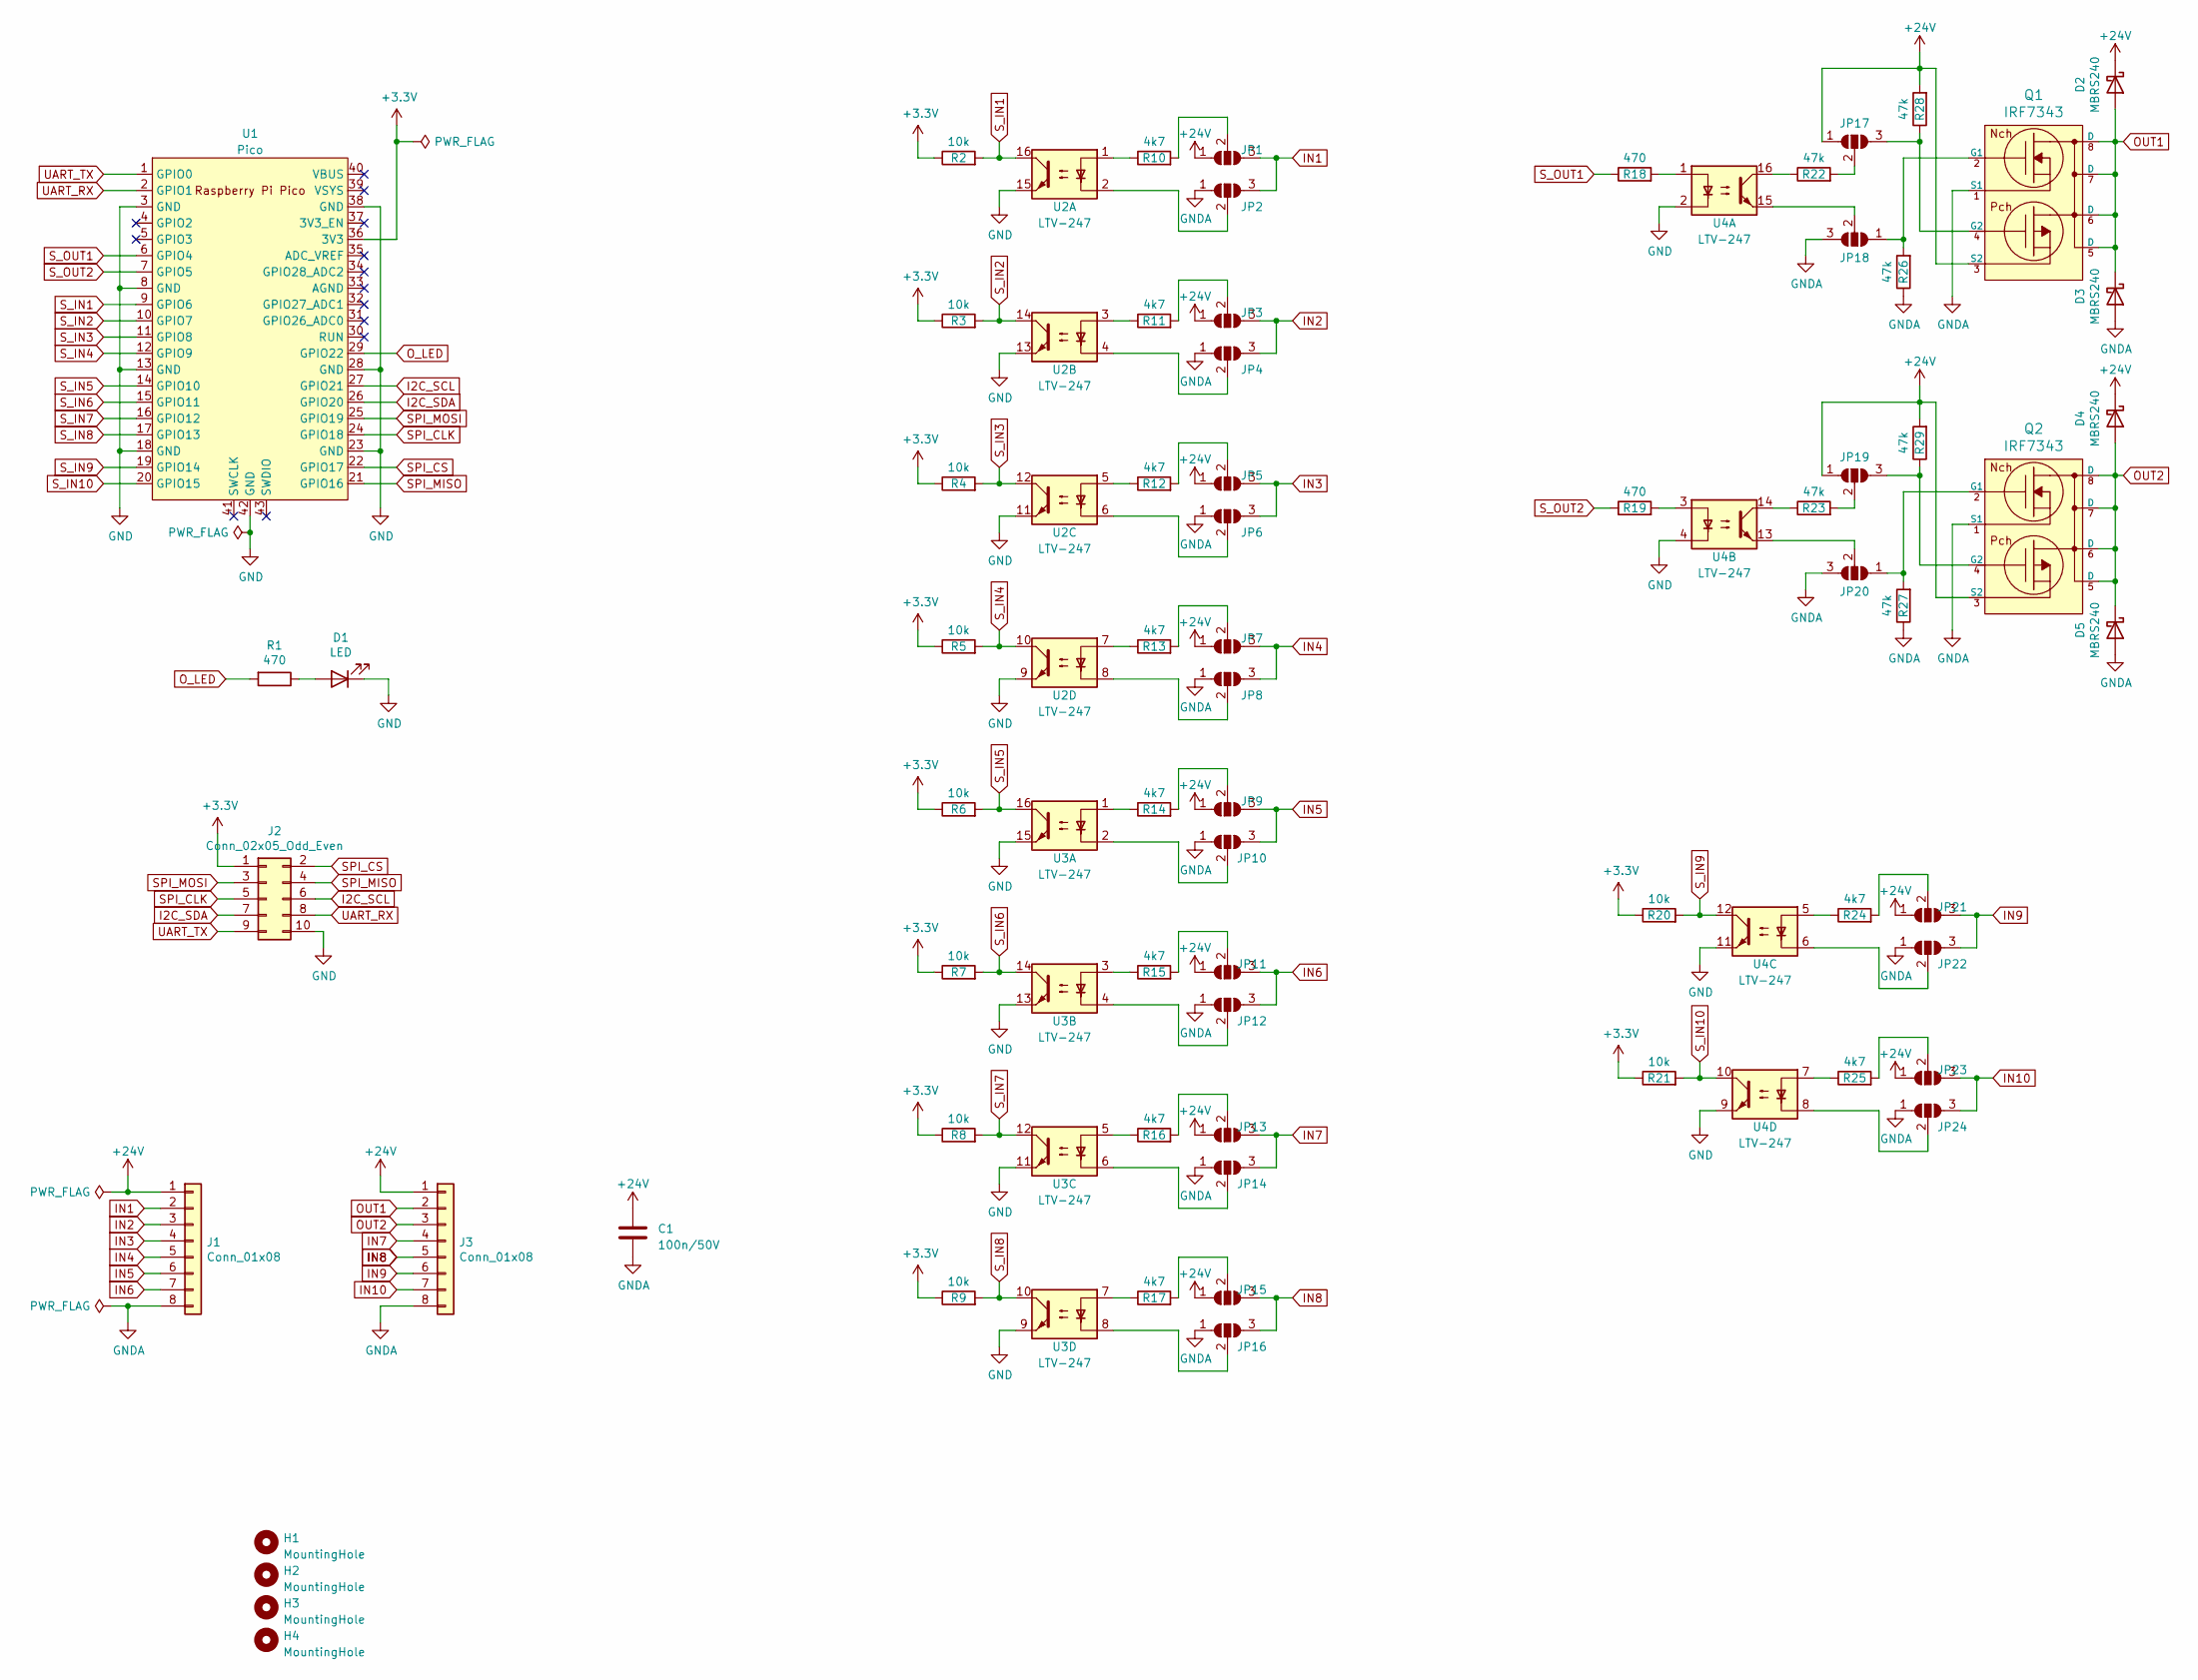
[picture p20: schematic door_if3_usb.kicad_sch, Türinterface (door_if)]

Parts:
C1: 100n/50V; C_0603_1608Metric_Pad1.08x0.95mm_HandSolder
D1: LED; LED_0603_1608Metric_Pad1.05x0.95mm_HandSolder
D2, D3, D4, D5: MBRS240; D_SMB_Handsoldering
H1, H2, H3, H4: MountingHole; MountingHole_3.2mm_M3_DIN965
J1, J3: Conn_01x08; LSA-IDC381-8
J2: Conn_02x05_Odd_Even; con-harting-ml-ML10
JP1, JP2, JP3, JP4, JP5, JP6, JP7, JP8, JP9, JP10, JP11, JP12, JP13, JP14, JP15, JP16, JP17, JP18, JP19, JP20, JP21, JP22, JP23, JP24: SolderJumper_3_Open; SolderJumper-3_P1.3mm_Open_Pad1.0x1.5mm
Q1, Q2: IRF7343; SO-8_3.9x4.9mm_P1.27mm
R1, R18, R19: 470; R_0603_1608Metric_Pad0.98x0.95mm_HandSolder
R2, R3, R4, R5, R6, R7, R8, R9, R20, R21: 10k; R_0603_1608Metric_Pad0.98x0.95mm_HandSolder
R10, R11, R12, R13, R14, R15, R16, R17, R24, R25: 4k7; R_0603_1608Metric_Pad0.98x0.95mm_HandSolder
R22, R23, R26, R27, R28, R29: 47k; R_0603_1608Metric_Pad0.98x0.95mm_HandSolder
U1: Pico; RPi_Pico_SMDonly
U2, U3, U4: LTV-247; SOP-16_4.4x10.4mm_P1.27mm

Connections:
+3V3: J2.1, R2.1, R3.1, R4.1, R5.1, R6.1, R7.1, R8.1, R9.1, R20.1, R21.1, U1.36 (3V3)
+24V: C1.1, D2.1 (K), D4.1 (K), J1.1, J3.1, JP1.1 (A), JP3.1 (A), JP5.1 (A), JP7.1 (A), JP9.1 (A), JP11.1 (A), JP13.1 (A), JP15.1 (A), JP17.1 (A), JP19.1 (A), JP21.1 (A), JP23.1 (A), Q1.3 (S2), Q2.3 (S2), R28.2, R29.2
GND: D1.1 (K), J2.10, U1.3 (GND), U1.8 (GND), U1.13 (GND), U1.18 (GND), U1.23 (GND), U1.28 (GND), U1.38 (GND), U1.42 (GND), U2.9, U2.11, U2.13, U2.15, U3.9, U3.11, U3.13, U3.15, U4.2, U4.4, U4.9, U4.11
GNDA: C1.2, D3.2 (A), D5.2 (A), J1.8, J3.8, JP2.1 (A), JP4.1 (A), JP6.1 (A), JP8.1 (A), JP10.1 (A), JP12.1 (A), JP14.1 (A), JP16.1 (A), JP18.3 (B), JP20.3 (B), JP22.1 (A), JP24.1 (A), Q1.1 (S1), Q2.1 (S1), R26.1, R27.1
I2C_SCL: J2.6, U1.27 (GPIO21)
I2C_SDA: J2.7, U1.26 (GPIO20)
IN1: J1.2, JP1.3 (B), JP2.3 (B)
IN2: J1.3, JP3.3 (B), JP4.3 (B)
IN3: J1.4, JP5.3 (B), JP6.3 (B)
IN4: J1.5, JP7.3 (B), JP8.3 (B)
IN5: J1.6, JP9.3 (B), JP10.3 (B)
IN6: J1.7, JP11.3 (B), JP12.3 (B)
IN7: J3.4, JP13.3 (B), JP14.3 (B)
IN8: J3.5, JP15.3 (B), JP16.3 (B)
IN9: J3.6, JP21.3 (B), JP22.3 (B)
IN10: J3.7, JP23.3 (B), JP24.3 (B)
unnamed: D1.2 (A), R1.1
unnamed: JP1.2 (C), R10.2
unnamed: JP2.2 (C), U2.2
unnamed: JP3.2 (C), R11.2
unnamed: JP4.2 (C), U2.4
unnamed: JP5.2 (C), R12.2
unnamed: JP6.2 (C), U2.6
unnamed: JP7.2 (C), R13.2
unnamed: JP8.2 (C), U2.8
unnamed: JP9.2 (C), R14.2
unnamed: JP10.2 (C), U3.2
unnamed: JP11.2 (C), R15.2
unnamed: JP12.2 (C), U3.4
unnamed: JP13.2 (C), R16.2
unnamed: JP14.2 (C), U3.6
unnamed: JP15.2 (C), R17.2
unnamed: JP16.2 (C), U3.8
unnamed: JP17.3 (B), Q1.4 (G2), R28.1
unnamed: JP17.2 (C), R22.2
unnamed: JP18.1 (A), Q1.2 (G1), R26.2
unnamed: JP18.2 (C), U4.15
unnamed: JP19.3 (B), Q2.4 (G2), R29.1
unnamed: JP19.2 (C), R23.2
unnamed: JP20.1 (A), Q2.2 (G1), R27.2
unnamed: JP20.2 (C), U4.13
unnamed: JP21.2 (C), R24.2
unnamed: JP22.2 (C), U4.6
unnamed: JP23.2 (C), R25.2
unnamed: JP24.2 (C), U4.8
unnamed: R10.1, U2.1
unnamed: R11.1, U2.3
unnamed: R12.1, U2.5
unnamed: R13.1, U2.7
unnamed: R14.1, U3.1
unnamed: R15.1, U3.3
unnamed: R16.1, U3.5
unnamed: R17.1, U3.7
unnamed: R18.2, U4.1
unnamed: R19.2, U4.3
unnamed: R22.1, U4.16
unnamed: R23.1, U4.14
unnamed: R24.1, U4.5
unnamed: R25.1, U4.7
OUT1: D2.2 (A), D3.1 (K), J3.2, Q1.5 (D), Q1.6 (D), Q1.7 (D), Q1.8 (D)
OUT2: D4.2 (A), D5.1 (K), J3.3, Q2.5 (D), Q2.6 (D), Q2.7 (D), Q2.8 (D)
O_LED: R1.2, U1.29 (GPIO22)
SPI_CLK: J2.5, U1.24 (GPIO18)
SPI_CS: J2.2, U1.22 (GPIO17)
SPI_MISO: J2.4, U1.21 (GPIO16)
SPI_MOSI: J2.3, U1.25 (GPIO19)
S_IN1: R2.2, U1.9 (GPIO6), U2.16
S_IN2: R3.2, U1.10 (GPIO7), U2.14
S_IN3: R4.2, U1.11 (GPIO8), U2.12
S_IN4: R5.2, U1.12 (GPIO9), U2.10
S_IN5: R6.2, U1.14 (GPIO10), U3.16
S_IN6: R7.2, U1.15 (GPIO11), U3.14
S_IN7: R8.2, U1.16 (GPIO12), U3.12
S_IN8: R9.2, U1.17 (GPIO13), U3.10
S_IN9: R20.2, U1.19 (GPIO14), U4.12
S_IN10: R21.2, U1.20 (GPIO15), U4.10
S_OUT1: R18.1, U1.6 (GPIO4)
S_OUT2: R19.1, U1.7 (GPIO5)
UART_RX: J2.8, U1.2 (GPIO1)
UART_TX: J2.9, U1.1 (GPIO0)

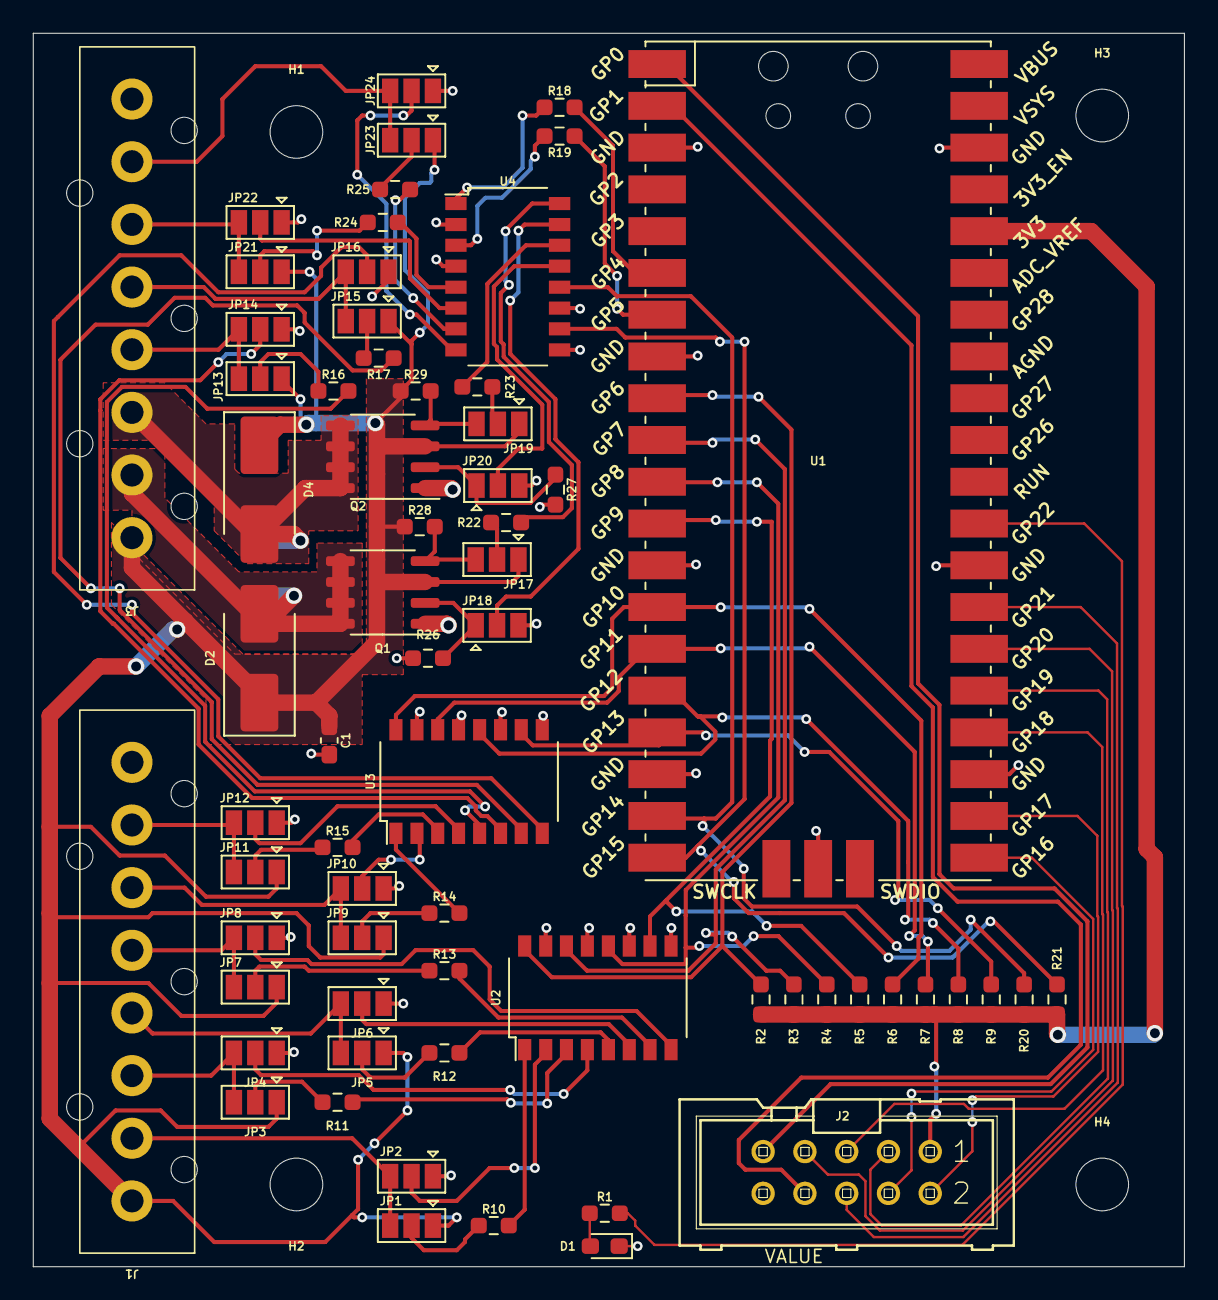
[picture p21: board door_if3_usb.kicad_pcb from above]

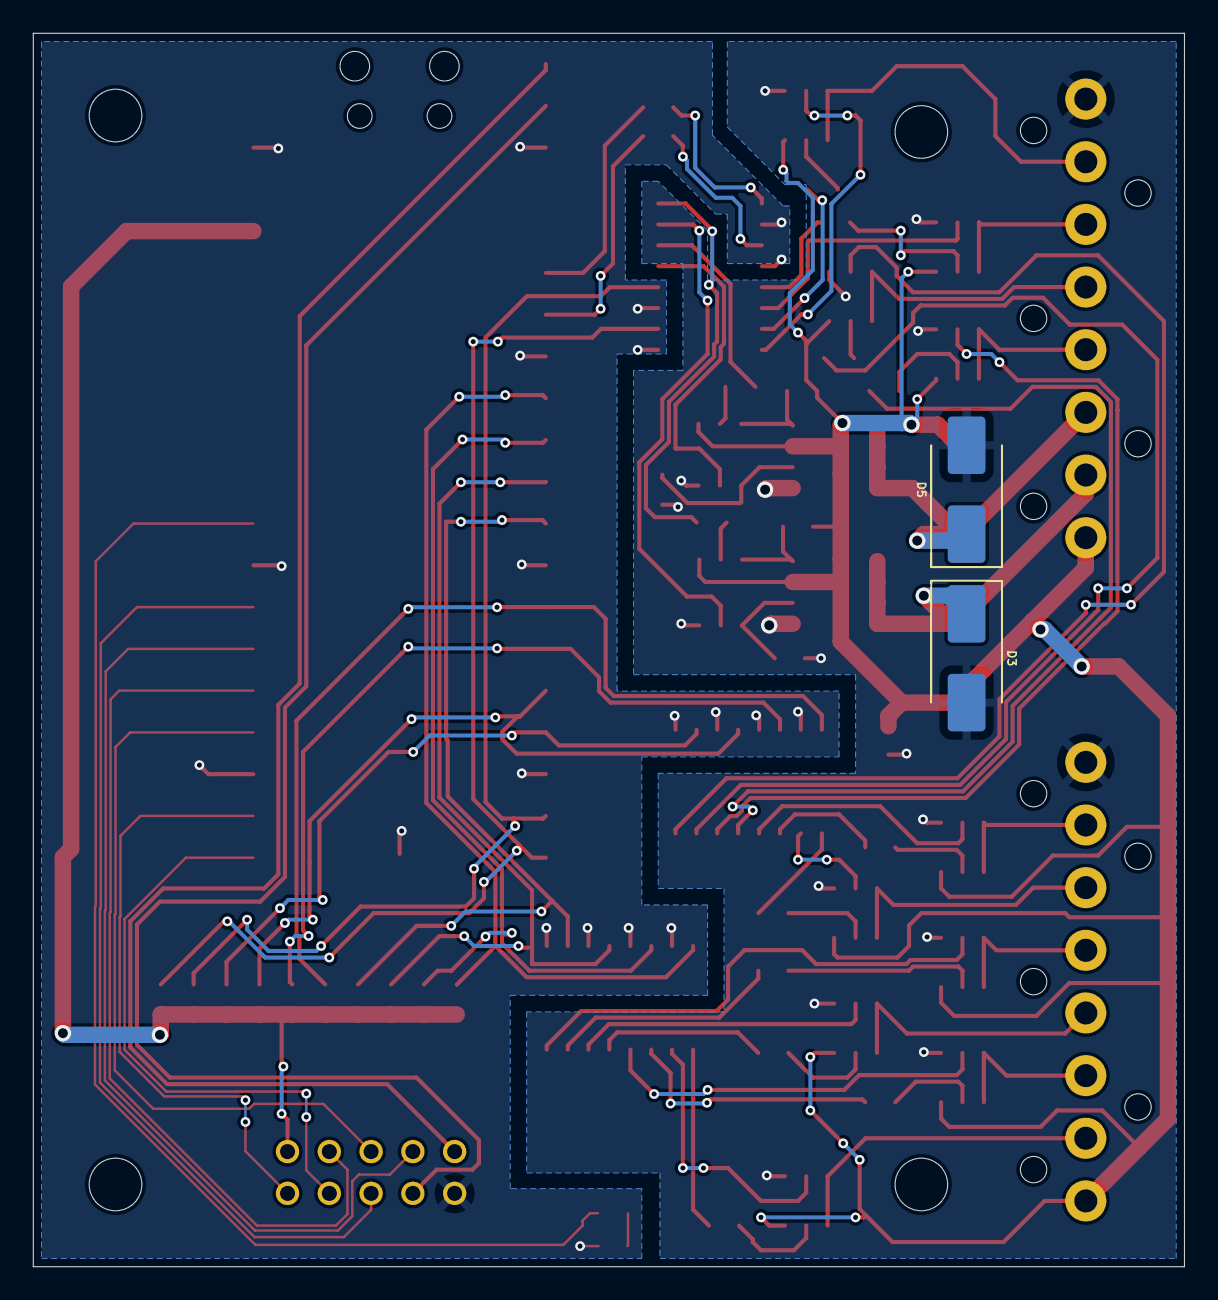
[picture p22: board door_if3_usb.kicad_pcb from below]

Board: 2 copper layers, 70.0 x 75.0 mm, 72 parts (2 on the bottom side), 80 nets.

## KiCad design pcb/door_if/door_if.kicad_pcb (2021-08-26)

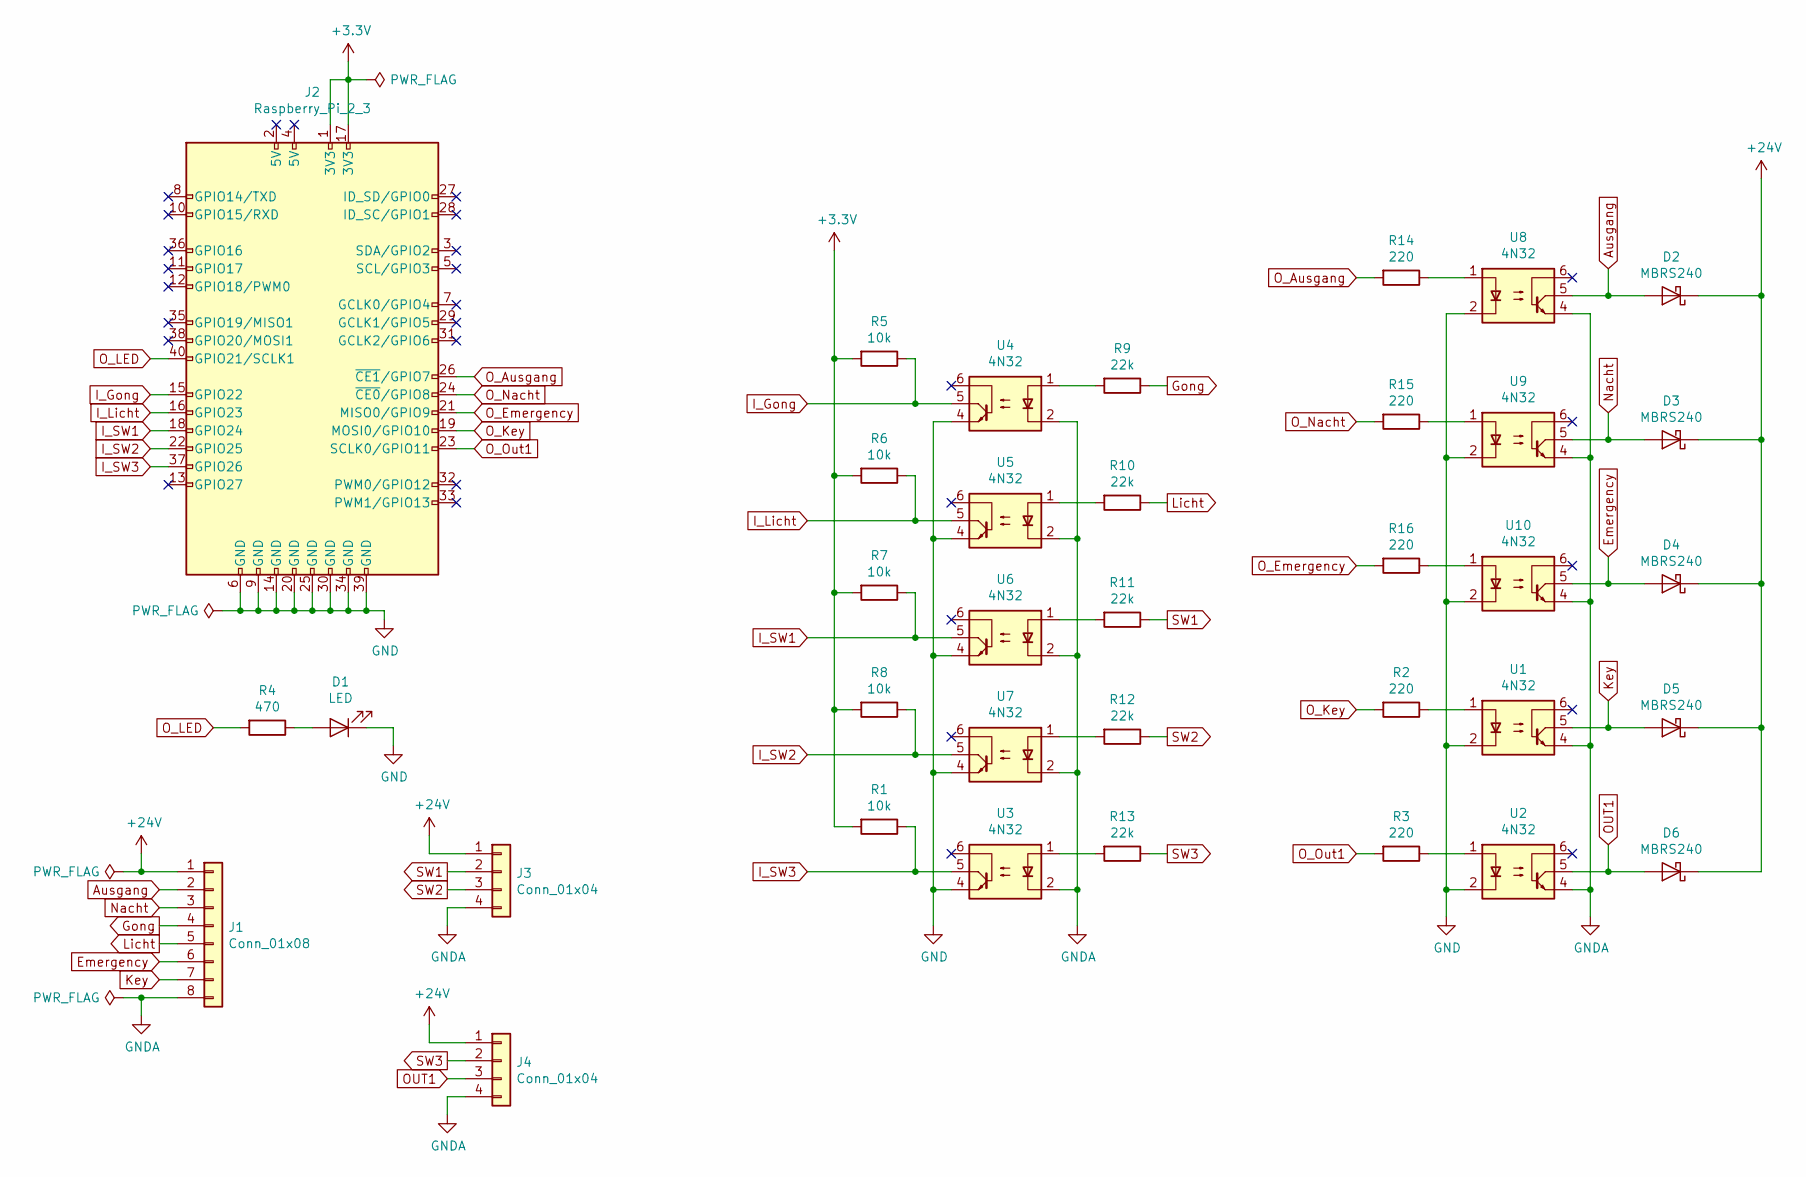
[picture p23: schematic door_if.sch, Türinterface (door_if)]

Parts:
D1: LED; LED_0603_1608Metric_Pad1.05x0.95mm_HandSolder
D2, D3, D4, D5, D6: MBRS240; D_SMB_Handsoldering
J1: Conn_01x08; con-ria-TYPE_182_169_8PIN
J2: Raspberry_Pi_2_3; CC_RPI_3_4
J3, J4: Conn_01x04; con-ria-TYPE_182_169_4PIN
R1, R5, R6, R7, R8: 10k; R_0603_1608Metric_Pad1.05x0.95mm_HandSolder
R2, R3, R14, R15, R16: 220; R_0603_1608Metric_Pad1.05x0.95mm_HandSolder
R4: 470; R_0603_1608Metric_Pad1.05x0.95mm_HandSolder
R9, R10, R11, R12, R13: 22k; R_0603_1608Metric_Pad1.05x0.95mm_HandSolder
U1, U2, U3, U4, U5, U6, U7, U8, U9, U10: 4N32; DIP-6_W7.62mm

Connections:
+3V3: J2.1 (3V3), J2.17 (3V3), R1.2, R5.2, R6.2, R7.2, R8.2
+24V: D2.1 (K), D3.1 (K), D4.1 (K), D5.1 (K), D6.1 (K), J1.1, J3.1, J4.1
Ausgang: D2.2 (A), J1.2, U8.5
Emergency: D4.2 (A), J1.6, U10.5
GND: D1.1 (K), J2.6 (GND), J2.9 (GND), J2.14 (GND), J2.20 (GND), J2.25 (GND), J2.30 (GND), J2.34 (GND), J2.39 (GND), U1.2, U2.2, U3.4, U4.4, U5.4, U6.4, U7.4, U8.2, U9.2, U10.2
GNDA: J1.8, J3.4, J4.4, U1.4, U2.4, U3.2, U4.2, U5.2, U6.2, U7.2, U8.4, U9.4, U10.4
Gong: J1.4, R9.1
I_Gong: J2.15 (GPIO22), R5.1, U4.5
I_Licht: J2.16 (GPIO23), R6.1, U5.5
I_SW1: J2.18 (GPIO24), R7.1, U6.5
I_SW2: J2.22 (GPIO25), R8.1, U7.5
I_SW3: J2.37 (GPIO26), R1.1, U3.5
Key: D5.2 (A), J1.7, U1.5
Licht: J1.5, R10.1
Nacht: D3.2 (A), J1.3, U9.5
unnamed: D1.2 (A), R4.1
unnamed: R2.1, U1.1
unnamed: R3.1, U2.1
unnamed: R9.2, U4.1
unnamed: R10.2, U5.1
unnamed: R11.2, U6.1
unnamed: R12.2, U7.1
unnamed: R13.2, U3.1
unnamed: R14.1, U8.1
unnamed: R15.1, U9.1
unnamed: R16.1, U10.1
OUT1: D6.2 (A), J4.3, U2.5
O_Ausgang: J2.26 (~CE1~/GPIO7), R14.2
O_Emergency: J2.21 (MISO0/GPIO9), R16.2
O_Key: J2.19 (MOSI0/GPIO10), R2.2
O_LED: J2.40 (GPIO21/SCLK1), R4.2
O_Nacht: J2.24 (~CE0~/GPIO8), R15.2
O_Out1: J2.23 (SCLK0/GPIO11), R3.2
SW1: J3.2, R11.1
SW2: J3.3, R12.1
SW3: J4.2, R13.1

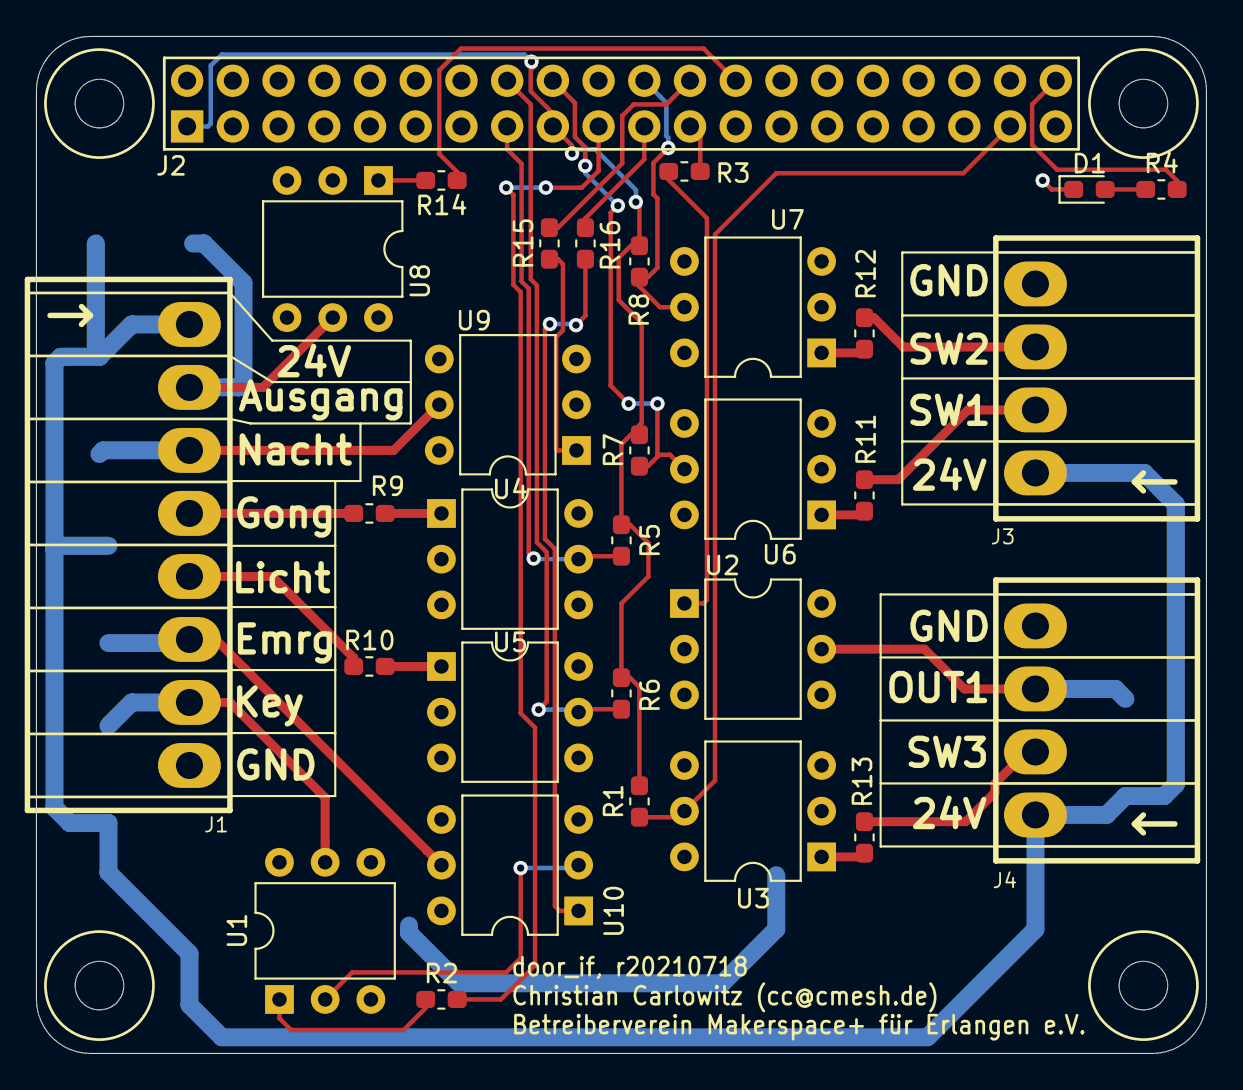
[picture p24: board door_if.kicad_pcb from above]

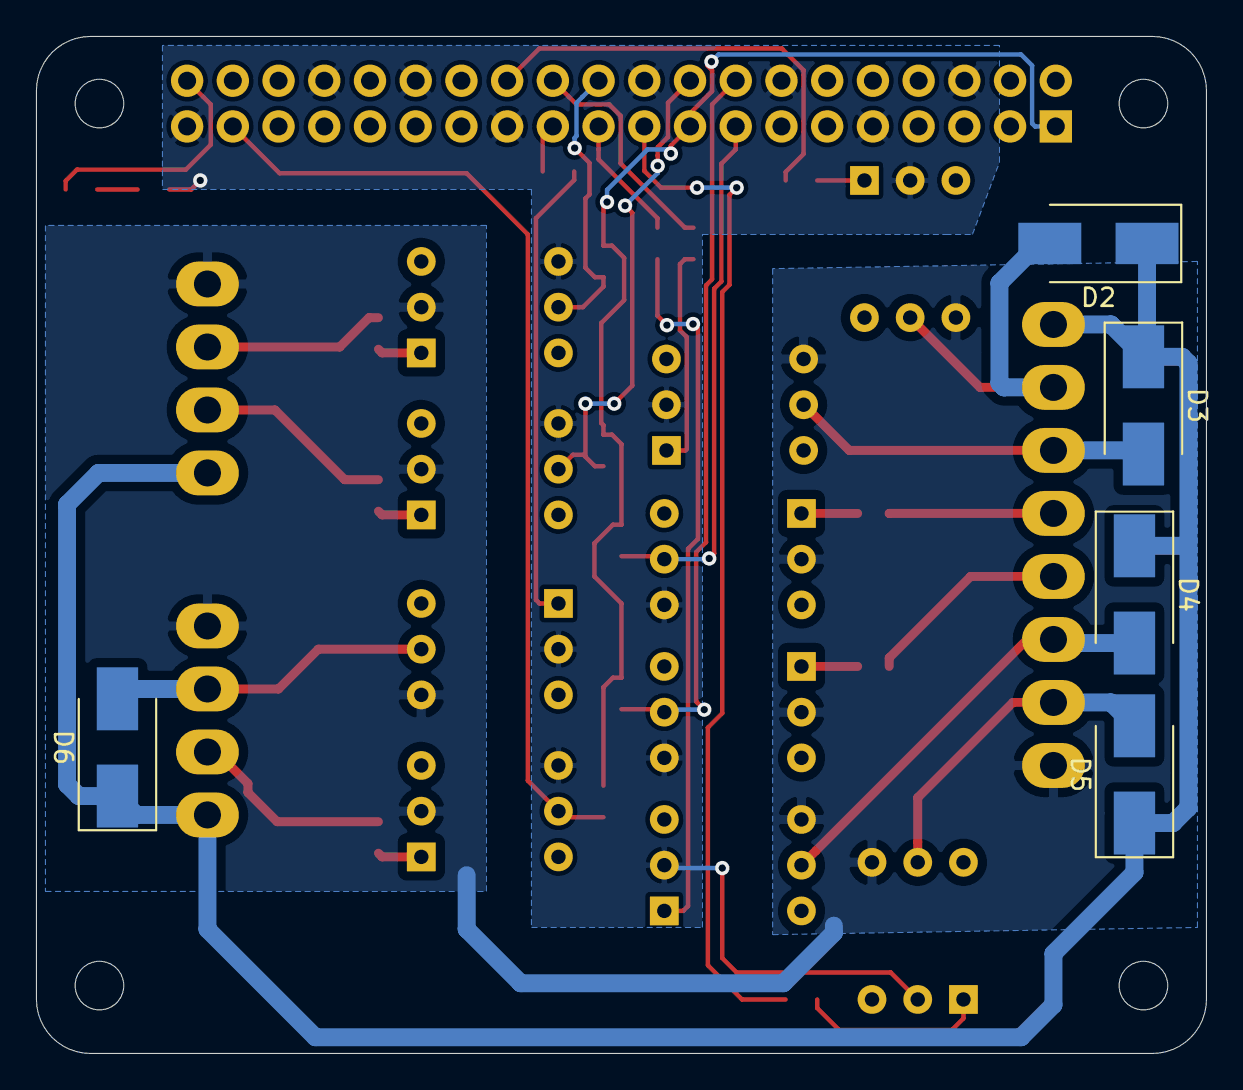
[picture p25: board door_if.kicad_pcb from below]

Board: 2 copper layers, 65.0 x 56.5 mm, 36 parts (5 on the bottom side), 36 nets.

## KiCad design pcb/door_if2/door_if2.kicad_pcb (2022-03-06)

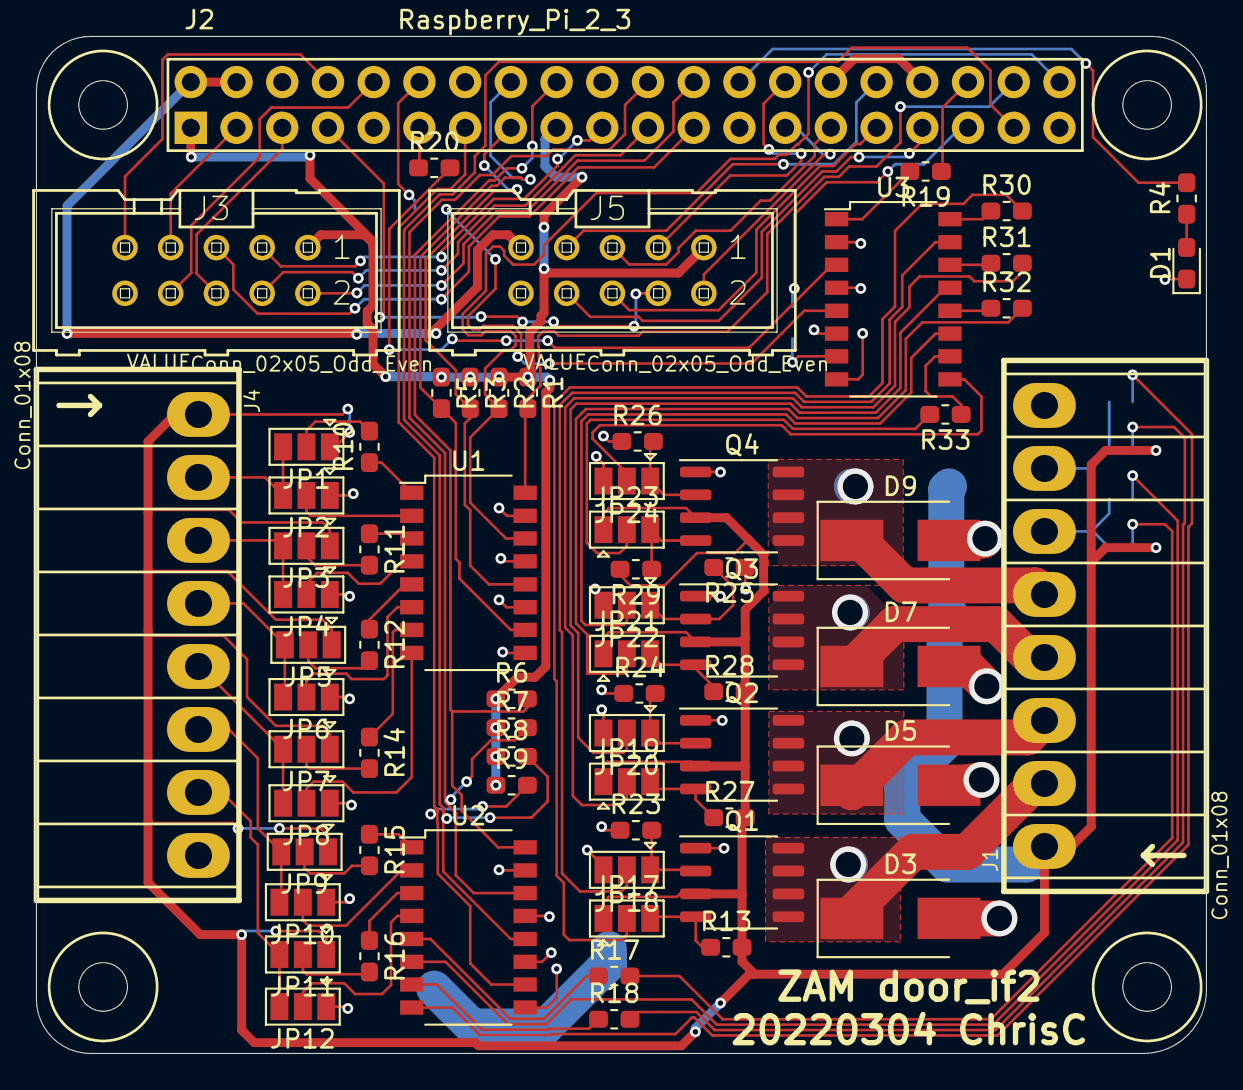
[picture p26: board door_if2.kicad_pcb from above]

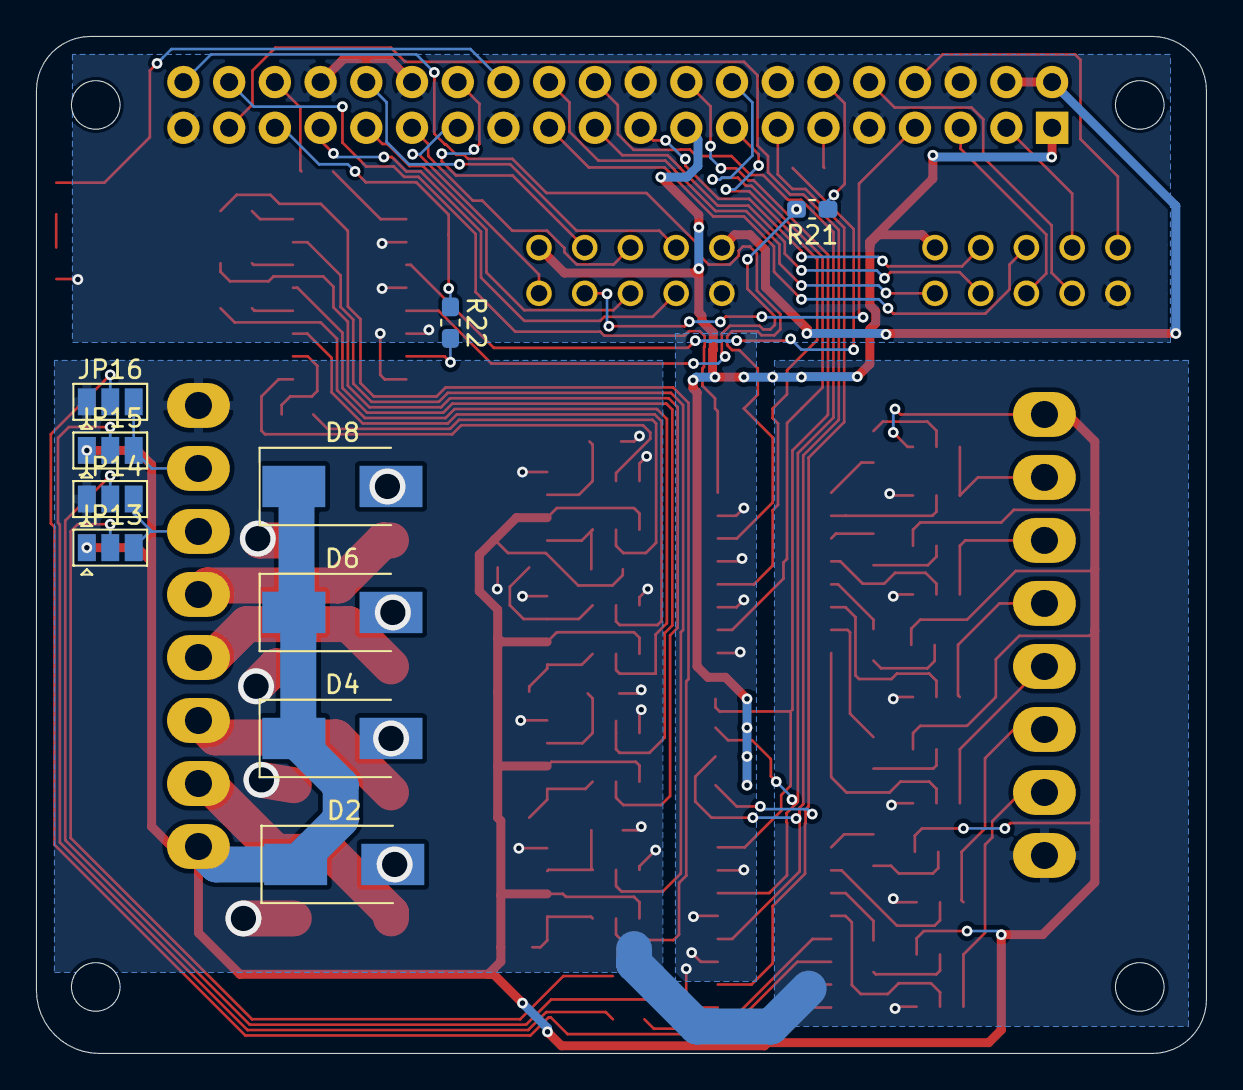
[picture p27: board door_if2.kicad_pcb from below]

Board: 2 copper layers, 65.0 x 56.5 mm, 78 parts (10 on the bottom side), 94 nets.

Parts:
D1: LED; LED_0603_1608Metric_Pad1.05x0.95mm_HandSolder
D2, D3, D4, D5, D6, D7, D8, D9: MBRS240; D_SMB_Handsoldering
J1, J4: Conn_01x08; con-ria-TYPE_182_169_8PIN
J2: Raspberry_Pi_2_3; CC_RPI_3_4
J3, J5: Conn_02x05_Odd_Even; con-harting-ml-ML10
JP1, JP2, JP3, JP4, JP5, JP6, JP7, JP8, JP9, JP10, JP11, JP12, JP13, JP14, JP15, JP16, JP17, JP18, JP19, JP20, JP21, JP22, JP23, JP24: SolderJumper_3_Open; SolderJumper-3_P1.3mm_Open_Pad1.0x1.5mm
Q1, Q2, Q3, Q4: IRF7343; SO-8_3.9x4.9mm_P1.27mm
R1, R2, R3, R5, R6, R7, R8, R9, R13, R23, R24, R25, R26, R27, R28, R29, R30, R31, R32, R33: 10k; R_0603_1608Metric_Pad1.05x0.95mm_HandSolder
R4: 470; R_0603_1608Metric_Pad1.05x0.95mm_HandSolder
R10, R11, R12, R14, R15, R16, R17, R18: 1k; R_0603_1608Metric_Pad1.05x0.95mm_HandSolder
R19, R20, R21, R22: 220; R_0603_1608Metric_Pad1.05x0.95mm_HandSolder
U1, U2, U3: LTV-247; SOP-16_4.4x10.4mm_P1.27mm

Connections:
+3V3: J2.1, J2.17, J3.1, J5.1, R1.1, R2.1, R3.1, R5.1, R6.1, R7.1, R8.1, R9.1
+5V: J2.2, J2.4, J5.9
+12V: D2.1, D4.1, D6.1, D8.1, J1.1, J4.1, JP1.1, JP3.1, JP5.1, JP7.1, JP9.1, JP11.1, JP13.1, JP15.1, JP17.1, JP19.1, JP21.1, JP23.1, Q1.3, Q2.3, Q3.3, Q4.3, R13.2, R27.2, R28.2, R29.2
GND: D1.1, J2.6, J2.9, J2.14, J2.20, J2.25, J2.30, J2.34, J2.39, J3.10, J5.10, U1.9, U1.11, U1.13, U1.15, U2.9, U2.11, U2.13, U2.15, U3.2, U3.4, U3.6, U3.8
GNDA: D3.2, D5.2, D7.2, D9.2, J1.8, J4.8, JP2.1, JP4.1, JP6.1, JP8.1, JP10.1, JP12.1, JP14.1, JP16.1, JP18.3, JP20.3, JP22.3, JP24.3, Q1.1, Q2.1, Q3.1, Q4.1, R23.1, R24.1, R25.1, R26.1
GPIO0: J2.27, J5.2
GPIO1: J2.28, J5.3
GPIO2: J2.7, J5.4
GPIO3: J2.29, J5.5
GPIO4: J2.31, J5.6
GPIO5: J2.32, J5.7
GPIO6: J2.33, J5.8
I2C_SCL: J2.5, J3.6
I2C_SDA: J2.3, J3.7
IN1: J4.2, JP1.3, JP2.3
IN2: J4.3, JP3.3, JP4.3
IN3: J4.4, JP5.3, JP6.3
IN4: J4.5, JP7.3, JP8.3
IN5: J4.6, JP9.3, JP10.3
IN6: J4.7, JP11.3, JP12.3
IN7: J1.6, JP13.3, JP14.3
IN8: J1.7, JP15.3, JP16.3
unnamed: D1.2, R4.1
unnamed: JP1.2, R10.2
unnamed: JP2.2, U1.2
unnamed: JP3.2, R11.2
unnamed: JP4.2, U1.4
unnamed: JP5.2, R12.2
unnamed: JP6.2, U1.6
unnamed: JP7.2, R14.2
unnamed: JP8.2, U1.8
unnamed: JP9.2, R15.2
unnamed: JP10.2, U2.2
unnamed: JP11.2, R16.2
unnamed: JP12.2, U2.4
unnamed: JP13.2, R17.2
unnamed: JP14.2, U2.6
unnamed: JP15.2, R18.2
unnamed: JP16.2, U2.8
unnamed: JP17.2, R30.2
unnamed: JP17.3, Q1.4, R13.1
unnamed: JP18.1, Q1.2, R23.2
unnamed: JP18.2, U3.15
unnamed: JP19.2, R31.2
unnamed: JP19.3, Q2.4, R27.1
unnamed: JP20.1, Q2.2, R24.2
unnamed: JP20.2, U3.13
unnamed: JP21.2, R32.2
unnamed: JP21.3, Q3.4, R28.1
unnamed: JP22.1, Q3.2, R25.2
unnamed: JP22.2, U3.11
unnamed: JP23.2, R33.2
unnamed: JP23.3, Q4.4, R29.1
unnamed: JP24.1, Q4.2, R26.2
unnamed: JP24.2, U3.9
unnamed: R10.1, U1.1
unnamed: R11.1, U1.3
unnamed: R12.1, U1.5
unnamed: R14.1, U1.7
unnamed: R15.1, U2.1
unnamed: R16.1, U2.3
unnamed: R17.1, U2.5
unnamed: R18.1, U2.7
unnamed: R19.2, U3.1
unnamed: R20.2, U3.3
unnamed: R21.2, U3.5
unnamed: R22.2, U3.7
unnamed: R30.1, U3.16
unnamed: R31.1, U3.14
unnamed: R32.1, U3.12
unnamed: R33.1, U3.10
OUT1: D2.2, D3.1, J1.2, Q1.5, Q1.6, Q1.7, Q1.8
OUT2: D4.2, D5.1, J1.3, Q2.5, Q2.6, Q2.7, Q2.8
OUT3: D6.2, D7.1, J1.4, Q3.5, Q3.6, Q3.7, Q3.8
OUT4: D8.2, D9.1, J1.5, Q4.5, Q4.6, Q4.7, Q4.8
O_LED: J2.26, R4.2
SPI_CLK: J2.23, J3.5
SPI_CS: J2.24, J3.2
SPI_MISO: J2.21, J3.4
SPI_MOSI: J2.19, J3.3
S_IN1: J2.38, R1.2, U1.16
S_IN2: J2.40, R2.2, U1.14
S_IN3: J2.15, R3.2, U1.12
S_IN4: J2.16, R5.2, U1.10
S_IN5: J2.18, R6.2, U2.16
S_IN6: J2.22, R7.2, U2.14
S_IN7: J2.37, R8.2, U2.12
S_IN8: J2.13, R9.2, U2.10
S_OUT1: J2.36, R19.1
S_OUT2: J2.11, R20.1
S_OUT3: J2.12, R21.1
S_OUT4: J2.35, R22.1
UART_RX: J2.10, J3.8
UART_TX: J2.8, J3.9

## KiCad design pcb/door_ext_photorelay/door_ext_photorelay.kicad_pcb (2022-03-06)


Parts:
C1, C2, C3, C4: 100n; C_0603_1608Metric_Pad1.05x0.95mm_HandSolder
H1, H2, H3, H4: MountingHole; MountingHole_3.2mm_M3
J1: Conn_02x04_Odd_Even; PinHeader_2x04_P2.54mm_Vertical
J2: Conn_02x05_Odd_Even; con-harting-ml-ML10
J3: Conn_01x08; con-ria-TYPE_182_169_8PIN
R1, R2, R3, R4, R5, R6, R7: R; R_0603_1608Metric_Pad1.05x0.95mm_HandSolder
RV1, RV2, RV3, RV4: R_POT; Potentiometer_Vishay_TS53YJ_Vertical
U1, U2, U3, U4: TS912; SO-8_3.9x4.9mm_P1.27mm
U6, U7, U8: TLP3555A; DIP-4_W8.89mm_SMDSocket_LongPads

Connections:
+3V3: C1.1, C2.1, C3.1, C4.1, J2.1, U1.8 (V+), U2.8 (V+), U3.8 (V+), U4.8 (V+)
/PD0: J1.2, R1.2, U1.2 (-)
/PD1: J1.4, R2.2, U2.2 (-)
/PD2: J1.6, R3.2, U3.2 (-)
/PD3: J1.8, R4.2, U4.2 (-)
GND: C1.2, C2.2, C3.2, C4.2, J1.1, J1.3, J1.5, J1.7, J2.10, RV1.3, RV2.3, RV3.3, RV4.3, U1.3 (+), U1.4 (V-), U2.3 (+), U2.4 (V-), U3.3 (+), U3.4 (V-), U4.3 (+), U4.4 (V-), U6.2, U7.2, U8.2
GPIO0: J2.2, R5.2
GPIO1: J2.3, R6.2
GPIO2: J2.4, R7.2
GPIO3: J2.5, RV1.1, U1.7
GPIO4: J2.6, RV2.1, U2.7
GPIO5: J2.7, RV3.1, U3.7
GPIO6: J2.8, RV4.1, U4.7
unnamed: J3.1, U6.3
unnamed: J3.2, U6.4
unnamed: J3.3, U7.3
unnamed: J3.4, U7.4
unnamed: J3.5, U8.3
unnamed: J3.6, U8.4
unnamed: R1.1, U1.1, U1.5 (+)
unnamed: R2.1, U2.1, U2.5 (+)
unnamed: R3.1, U3.1, U3.5 (+)
unnamed: R4.1, U4.1, U4.5 (+)
unnamed: R5.1, U6.1
unnamed: R6.1, U7.1
unnamed: R7.1, U8.1
unnamed: RV1.2, U1.6 (-)
unnamed: RV2.2, U2.6 (-)
unnamed: RV3.2, U3.6 (-)
unnamed: RV4.2, U4.6 (-)


Board: 2 copper layers, 57.0 x 47.0 mm, 29 parts (0 on the bottom side), 30 nets.

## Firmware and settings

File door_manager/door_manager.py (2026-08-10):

#!/usr/bin/env -S python3 -u

# This file is part of door_manager.
#
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
''' door_manager

Usage:
  door_manager.py [-c FILE]
  door_manager.py [-c FILE] (-s | --simulate)

Options:
  -s --simulate     Use console I/O for HAL instead of RPi GPIOs
  -c FILE           Use this config file (json) instead of ./config.json
'''

import logging
from json import loads
import datetime
import sys
import asyncio
from time import time
from signal import signal, SIGUSR1, SIGTERM

from docopt import docopt
from decorated_paho_mqtt import GenericMqttEndpoint

from door_hal import DoorHalRaspi, DoorHalUSB, DoorHalSim, HalConfig, GPIOHAL


FORMAT = '%(asctime)s %(processName)s#%(process)d @ %(module)s:%(name)s:%(funcName)s: %(message)s (%(filename)s:%(lineno)s)'
logging.basicConfig(format=FORMAT, handlers=[logging.StreamHandler()], level="INFO")
log = logging.getLogger(__name__)
mqtt_log = logging.getLogger(__name__ + ".mqtt")
mqtt_log.setLevel("DEBUG")


dormakabaMapping = {"in1": "sabotage", "in2": "entriegelt", \
    "in3": "verriegelt", "in4": "druecker", "in5": "steuerfalle", \
    "in6": "daueroffen"}

class DoorManager(GenericMqttEndpoint):
    def __init__(self, config, hal: GPIOHAL):
        # super().__init__ accesses self.door_id to build the endpoint.
        self.door_id=config['door-id']
        super().__init__(
            config['mqtt']['client_kwargs'],
            config['mqtt']['password_auth'],
            config['mqtt']['server_kwargs'],
            config['mqtt']['tls'])
        self.config = config
        self.hal: GPIOHAL = hal
        self.program = config.get("startup-program", "closed")


    @GenericMqttEndpoint.subscribe_decorator(lambda self: f'door/{self.door_id}/+', qos=2)
    def msg(self, cmd, *, client, userdata, message):
        if cmd == "open":
            self.open(client, userdata, message)
        else:
            log.error("Unknown command: " + cmd)

    def open(self, client, userdata, message):
        log.info("Received request to open door")
        # noinspection PyBroadException
        try:
            payload = loads(message.payload)
            assert 'not_after' in payload
            not_after = payload['not_after']
            now = time()
            if now < float(not_after):
                self.open_door()
            else:
                time_obj = datetime.datetime.fromtimestamp(not_after, datetime.timezone.utc)
                time_str = time_obj.strftime('%Y-%m-%dT%H:%M:%SZ')
                log.warning(f"Ignored delayed request, is only valid until {time_str}")
        except:
            log.error("Failed to parse request", exc_info=True)

    def _on_log(self, client, userdata, level, buf):
        mqtt_log.log(level, buf, extra=dict(client=client, userdata=userdata))

    def set_program(self, program):
        if program not in self.config["programs"]:
            log.error("Requested unknown door program: " + program)
        self.output_program(program)
        self.program = program

    def cycle_program(self, direction=1):
        """cycle forward (direction=1) or backward through the states (direction=-1)"""
        # when in a not-cycleable state, initialize to first
        if self.program not in self.config["cycle-programs"]:
            self.set_program(self.config["cycle-programs"][0])
            return
        ind = self.config["cycle-programs"].index(self.program)
        ind = (ind + direction) % len(self.config["cycle-programs"])
        self.set_program(self.config["cycle-programs"][ind])

    def open_door(self):
        for (pin, state) in self.config['open-gpios'].items():
            self.hal.impulse(pin, state, self.config['open-time'])

    def output_program(self, program):
        # turn everything off
        s = set()
        for gpios in self.config["programs"].values():
            s.update(gpios.keys())
        for gpio in s:
            val = "Z"
            if "inactive-outputs" in self.config:
                val = self.config["inactive-outputs"].get(gpio, self.config["inactive-outputs"].get("others","Z"))
            self.hal.setOutput(gpio, val)
        # enable the gpios for the program
        for (gpio, val) in self.config["programs"][program].items():
            self.hal.setOutput(gpio, val)

    async def cycle_loop(self):
        self.output_program(self.program)
        f = self.config["cycle-forward-input"]
        b = self.config.get("cycle-backward-input")
        can_cycle_backwards = b is not None
        fl = self.config.get("cycle-forward-input-level", "H")
        bl = self.config.get("cycle-backward-input-level", "H")
        inputs = {}
        while asyncio.get_running_loop().is_running():
            event = self.hal.getEvent()
            if event is None:
                await asyncio.sleep(0.5)
                continue
            prev_inputs = inputs
            inputs = loads(event)

            if inputs[f] == fl and not prev_inputs.get(f) == fl:
                self.cycle_program(1)
            if can_cycle_backwards and inputs[b] == bl and not prev_inputs.get(b) == bl:
                self.cycle_program(-1)

    async def switch_loop(self):
        while asyncio.get_running_loop().is_running():
            val = self.hal.getInput(self.config['switch-input'])
            program = self.config['switch-programs'][val]
            self.set_program(program)
            await asyncio.sleep(1)

    async def presence_loop(self):
        gpioPresence = self.config["presence-gpio"]
        gpioPresenceInv = self.config["presence-gpio-inverted"]
        while asyncio.get_running_loop().is_running():
            try:
                presence = self.hal.getInput(gpioPresence)
                if gpioPresenceInv:
                    presence = not presence
                self.publish("door/+/presence", self.door_id, qos=2, retain=True, payload=str(presence).lower())
            except:
                log.error("Failed to retrieve or publish inputs", exc_info=True)
            await asyncio.sleep(5)


    async def dormakaba_open_loop(self):
        while asyncio.get_running_loop().is_running():
            try:
                isOpen = (not self.hal.getInput("in2")) or self.hal.getInput("in5")
                self.publish("door/+/is_open", self.door_id, qos=2, retain=True, payload=str(isOpen).lower())
                log.info("door status is_open=" + str(isOpen))

                for k in dormakabaMapping.keys():
                    name = dormakabaMapping[k]
                    if self.hal.exist(k):
                        val = self.hal.getInput(k)
                        self.publish("door/+/input_%s" % name, \
                            self.door_id, qos=2, retain=True, \
                                payload=str(val).lower())
            except:
                log.error("Failed to retrieve or publish inputs for dormakaba_open_loop", exc_info=True)
            await asyncio.sleep(5)

    async def usb_push_pinstatus(self):
        ev = self.hal.getEvent()
        if ev is not None:
            log.info("usb_push_instatus: got %s" % ev)
        await asyncio.sleep(0.2)

    def gong_handler(self, v):
        try:
            self.publish("door/+/gong", self.door_id, qos=2, retain=False)
        except:
            log.error("Failed publishing gong", exc_info=True)


    def start(self, loop):
        self.connect()
        if self.config.get("program-change", None) == "cycle":
            loop.create_task(self.cycle_loop())
        if self.config.get("program-change", None) == "switch":
            loop.create_task(self.switch_loop())

        if "input-type" in self.config:
            if self.config["input-type"] == "gildor":
                self.hal.registerInputCallback("gong", self.gong_handler, falling=False)
                loop.create_task(self.presence_loop())
            elif self.config["input-type"] == "dormakaba":
                loop.create_task(self.dormakaba_open_loop())
            elif self.config["input-type"] == "dormakaba_ed_100_250":
                loop.create_task(self.usb_push_pinstatus())

def main():
    args = docopt(__doc__)
    print(args)
    config_path = args["-c"]
    if config_path is None: config_path = "./config.json"
    with open(config_path) as fd:
        config = loads(fd.read())
    if "loglevel" in config:
        mqtt_log.setLevel(config["loglevel"])

    def sigterm_handler(signum, frame):
        dm._mqttc.loop_stop()
        hal.cleanup()
        sys.exit(0)

    def sigusr1_handler(signum, frame):
        dm.open_door()

    signal(SIGUSR1, sigusr1_handler)
    signal(SIGTERM, sigterm_handler)


    if config["gpio-config"] == "usb":
        halcfg = HalConfig()
        halcfg.usbpath = config["usb-path"]
    else:
        halcfg = HalConfig(config["gpio-config"])

    if args['--simulate']:
        log.warning("Running in simulation mode")
        hal = DoorHalSim(halcfg)
    else:
        if config["gpio-config"] == "usb":
            hal = DoorHalUSB(halcfg)
        else:
            hal = DoorHalRaspi(halcfg)

    loop = asyncio.new_event_loop()
    dm = DoorManager(config, hal)
    dm.start(loop)
    loop.run_forever()

if __name__ == '__main__':
    main()

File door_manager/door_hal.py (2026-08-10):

# This file is part of door_manager.
#
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
from os import kill, getpid
from signal import SIGTERM
from time import sleep
from json import load, loads, JSONDecodeError
import queue
from threading import Lock
import abc
import functools


class HalConfig:
    def __init__(self, fname=None):
        if fname is None:
            self.inputs = {}
            self.outputs = {}
        else:
            with open(fname, "r") as f:
                cfgGpio = load(f)
            self.inputs = cfgGpio["inputs"]
            self.outputs = cfgGpio["outputs"]


class GPIOHAL(abc.ABC):
    def __init__(self, _cfg):
        pass

    @abc.abstractmethod
    def impulse(self, name, val, duration=2.0):
        pass

    @abc.abstractmethod
    def setOutput(self, name, val):
        pass

    @abc.abstractmethod
    def getInput(self, name):
        pass

    @abc.abstractmethod
    def getEvent(self):
        pass

    def cleanup(self):
        pass


class DoorHalRaspi(GPIOHAL):
    def __init__(self, cfg):
        import RPi.GPIO as gpio
        self.cfg = cfg
        self.gpio = gpio
        self.gpio.setmode(gpio.BCM)
        self.gpio.setwarnings(False)
        self.eventq = queue.Queue()
        self.callbacks = {}

        for i in self.cfg.inputs:
            self.gpio.setup(self.cfg.inputs[i], self.gpio.IN)
        for o in self.cfg.outputs:
            self.gpio.setup(self.cfg.outputs[o], self.gpio.OUT, initial=0)
        self.outputStates = {}
        for input in self.cfg.inputs:
            self.gpio.add_event_detect(
                self.cfg.inputs[input],
                self.gpio.BOTH,
                callback=functools.partial(self._event_callback, input),
                bouncetime=50)

    def _event_callback(self, input, *_args):
        pinval = self.gpio.input(self.cfg.inputs[input])
        if pinval:
            x = "H"
        else:
            x = "L"
        self.eventq.put({input: x})
        for cb in self.callbacks.get((input, x), ()):
            cb()

    def registerInputCallback(self, input, callback, falling=True):
        if falling is True:
            x = "L"
        elif falling is False:
            x = "H"
        else:
            raise TypeError("parameter falling should be True or False")
        if (input, x) not in self.callbacks:
            self.callbacks[(input, x)] = []
        self.callbacks[(input, x)].append(callback)

    def exist(self, name):
        return name in self.cfg.inputs

    def impulse(self, name, val, duration=2.0):
        reset = self.outputStates.get(name, "L")
        self.setOutput(name, val)
        sleep(duration)
        self.setOutput(name, reset)

    def setOutput(self, name, val):
        # TODO: ValueError instead of assert
        if val not in "HL":
            raise ValueError("GPIO value must be H or L. Unsupported value: %r" % val)
        assert (name in self.cfg.outputs)
        print('output', val, 'on', name)
        self.gpio.output(self.cfg.outputs[name], {"H": True, "L": False}[val])
        self.outputStates[name]=val

    def getInput(self, name):
        assert name in self.cfg.inputs
        return self.gpio.input(self.cfg.inputs[name]) == self.gpio.HIGH

    def getEvent(self):
        try:
            return self.eventq.get(block=False)
        except queue.Empty:
            return None

    def cleanup(self):
        self.gpio.cleanup()


class DoorHalUSB(GPIOHAL):
    def __init__(self, cfg):
        import serial
        self.cfg = cfg
        self.s = serial.Serial(cfg.usbpath, timeout=10)
        self.slock = Lock()
        self.eventq = queue.Queue()

        iv = self.getInputAll()
        for i in iv:
            self.cfg.inputs[i] = i

    def __readline(self, event_only=False):
        l = self.s.readline().strip().decode()
        while l.startswith("!"):
            self.eventq.put(l)
            if event_only:
                return None
            l = self.s.readline().strip().decode()
        return l

    def __checkok(self):
        l = self.__readline()
        assert l == "ok"

    def getEvent(self):
        with self.slock:
            if self.s.in_waiting > 0:
                self.__readline(event_only=True)
            if not self.eventq.empty():
                return self.eventq.get()[1:]
        return None  # no event pending

    def exist(self, name):
        return name in self.cfg.inputs

    def impulse(self, name, val, duration=None):
        assert val in "HLZ"
        with self.slock:
            cmd = "*impulse {name} {val}".format(name=name, val=val)
            if duration is not None:
                cmd += " {}".format(duration)
            self.s.write((cmd + "\r").encode())
            self.__checkok()

    def getInput(self, name):
        iv = self.getInputAll()
        assert name in iv
        return iv[name]

    def getInputAll(self):
        with self.slock:
            self.s.write("*read\r".encode())
            try:
                d = self.__readline()
                j = loads(d)
                return j
            except JSONDecodeError:
                print("JSONDecodeError")
            except TimeoutError:
                print("TimeoutError")
            except Exception as e:
                print("Exception:", str(e))

    def setOutput(self, name, val):
        assert val in "HLZ"
        with self.slock:
            self.s.write(("*set " + name + " " + val + "\r").encode())
            self.__checkok()
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

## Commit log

2021-08-26 added PCB design for door interface and RasPi setup instructions
    [door_if.kicad_pcb, door_if.sch]
2021-09-03 add logging and fix docopt requirement
    [door_manager.py]
2021-09-03 fixed env, explicity stop mqtt loop
    [door_manager.py]
2021-09-03 cleanup gpio thread
2021-10-22 fixed door presence pin interpretation and json compatibility
    [door_hal.py, door_manager.py]
2021-10-22 added door_if revision with open collector input driver support
    [door_if.kicad_pcb, door_if.sch]
2022-02-26 added door_if2
    [door_if2.kicad_pcb, door_if2.sch]
2022-03-06 added boards
    [door_ext_photorelay-B_Cu.gbr, door_ext_photorelay-B_Mask.gbr, door_ext_photorelay-B_SilkS.gbr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]
2022-08-12 moved pcbs to subfolder
    [door_ext_photorelay-B_Cu.gbr, door_ext_photorelay-B_Mask.gbr, door_ext_photorelay-B_SilkS.gbr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]
2022-08-12 fixed door manager for new hal abstraction
    [door_hal.py, door_manager.py]
2022-08-19 refactored door-manager input setup, added missing example entries for config
    [door_manager.py]
2023-03-24 added door if pcb version 3
    [door_if3_usb-B_Cu.gbl, door_if3_usb-B_Mask.gbs, door_if3_usb-B_Silkscreen.gbo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]
2023-03-27 output all input states on mqtt, fixed sim mode
    [door_hal.py, door_manager.py]
2023-03-27 added missing connection plan for switch version
2023-07-05 added machine variant of if3_usb
    [door_if3_usb_machine.kicad_pcb, door_if3_usb_machine.kicad_sch]
2023-07-06 completed if3_usb_machine
    [door_if3_usb_machine.kicad_pcb, door_if3_usb_machine.kicad_sch]
2023-07-07 finalized if3_usb_machine pcb
    [door_if3_usb_machine-B_Cu.gbl, door_if3_usb_machine-B_Mask.gbs, door_if3_usb_machine-B_Silkscreen.gbo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]
2023-07-12 added case designs
    [if3-usb-case.FCStd, raspi-hub-case.FCStd]
2023-09-03 added relais mount
    [relais_mount-CounterBlock.stl, relais_mount-Plate.stl, relais_mount.FCStd]
2023-09-15 fixed bug with decorator
    [door_manager.py]
2023-11-01 added door_if4 design
    [door_if4_usb.kicad_pcb, door_if4_usb.kicad_sch, door_if4_usb_inch2.kicad_sch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]
2023-11-03 almost completed door_if4_usb for manufacturing
    [Sample-BOM_JLCSMT.xlsx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]
2023-11-27 added final if4 design
    [0_bom.csv, 0_bom.xlsx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]
2023-11-28 added case design for if4
    [DINrail_Clip.fcstd, DINrail_Clip.stl, if4-usb-case.FCStd]
2023-11-28 if4 case height fix
    [if4-usb-case.FCStd]
2023-12-15 added new if4 case
    [if4-usb-case.v2.FCStd]
2023-12-15 increased clamp thickness in if4 case
    [if4-usb-case.v2.FCStd]
2023-12-15 added if4 case stl
    [if4-usb-case.v2.stl]
2023-12-27 added v2 of if4 board
    [0_bom.xlsx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]
2024-02-06 added pcb test program
2024-02-13 debug/bugfixes for new usb controller
    [door_hal.py, door_manager.py]
2024-07-10 Pi4 case for DIN
    [Pi4_DIN_case.stl, Pi4_DIN_case_2.stl]
2024-07-10 Added original lit
    [General_lit.stl]
2025-05-21 add "switch" mode for program change to implement the day/night switches
2025-07-30 resolve deprecation: split differenciate get_event_loop calls
    [door_manager.py]
2025-08-13 fix missiong -c in commandline parsing
    [door_manager.py]
2025-08-25 changes required for fail-open and active low buttons
    [door_manager.py]

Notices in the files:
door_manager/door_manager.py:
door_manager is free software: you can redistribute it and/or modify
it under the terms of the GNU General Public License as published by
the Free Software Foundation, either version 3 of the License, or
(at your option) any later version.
